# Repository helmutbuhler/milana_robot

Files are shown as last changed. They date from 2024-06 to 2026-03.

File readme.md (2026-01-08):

# Milana - A Two-Wheeled Jumping Robot

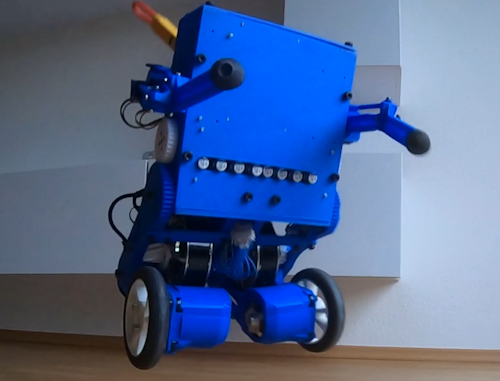
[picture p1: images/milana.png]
Milana


## Overview
Milana is a small and relatively cheap robot on two wheels. For a general description on how I built this robot, see [here](blog_post.md)

The robot has 6 motors on each side:
 - A BDC 280KV motor controlling the wheel.
 - A BDC 100KV motor controlling the knee (used for jumping).
 - A 35kg servo motor controlling the hip.
 - 3 1.5kg small servo motors, controlling the arm.

The brushless motors are controlled with two [ODrives](https://odriverobotics.com/), each with custom firmware to enable some of the tricks demonstrated in the [video](https://www.youtube.com/watch?v=lOAjTAtRaGs). All motors, except for the arm motors, also have precise encoders attached.
The robot is powered by two 3Ah 3S Lipo batteries and controlled by a Jetson Nano. The Jetson Nano is running custom control software on Ubuntu with a slightly modified Linux kernel. Beside the ODrives, the Jetson Nano is connected to the following:
 - IMU sensor for 3D Orientation.
 - Servo Driver to control all servo motors.
 - A2D Converter for battery charge measurement.
 - Microphone and speaker.

## Control
The robot can be controlled externally using various methods:
 - With custom software (Control UI), running on a separate computer and connected via Wifi. This can also be used to tune and calibrate internal parameters, debug issues and simulate certain parts of the robot.
 - With a wireless XBox controller.
 - With speech recognition and a [LLM](https://www.youtube.com/watch?v=1e_AJBxF1MY). The robot can reply using speech synthesis and execute a number of commands.

 ## Abilities
 The robot can...
 - balance on its wheels while driving and changing its body posture.
 - move its "knees" so fast that it will jump a few centimeters.
 - control each arm with 3 degrees of freedom and pick up light objects with them.
 - move up to about 10 km/h.
 - keep balance while moving with one wheel on a small ramp.

## Code
This robot is completely Open Source: The code for the "brain" of the robot is in this repository [in the robot folder](robot/). The software to control and debug the robot, [Control UI](control_ui/), is also here. There are also modules for [Automatic Speech Recognition](asr/), [Large Language Model](llm/) and [Text To Speech](tts/) included here that can optionally be used to have a conversation with the robot. Some of the code is in other repositories: The custom image for the Jetson Nano is [here](https://github.com/helmutbuhler/jetson_nano_image_milana). And the custom firmware image for the ODrives is [here](https://github.com/helmutbuhler/odrive_milana). All of these links point to a readme with more information about each component.

## Building
The CAD files and the meshes that need to be printed with a 3D printer are [here](CAD/). Other things that you need to buy are listed in the [Bill of Materials](extras/BOM.ods) (the total is about 1200€). [Here](images/) are some photos of the completed robot with some annotations for reference. More detailed information about each part is also in the comments of the code that controls it. 

This is not a project for beginners. If you intend to make the robot, some experience in robotics and coding is recommended. I also don't provide any warranty of any kind. Use all of this at your own risk.

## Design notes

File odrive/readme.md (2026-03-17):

# ODrive
## Overview
This robot uses two ODrives to control the 4 BLDC Motors that control the feet and leg motors. Some modifications were required to the Firmware, which you can find [here](https://github.com/helmutbuhler/odrive_milana). Clone that repository into the user home folder on the Jetson and flash the Firmware onto the ODrives (instructions are there).

The ODrive connected to the leg motors is located in the front of the robot (opposite of batteries). To connect to it with ODrivetool via UART, use this:
```
python3 ~/odrive_milana/tools/odrivetool --path serial:/dev/ttyTHS1_921600_8N2
```
Its axis numbers are: left=1 right=0

The ODrive connected to the foot motors is located in the back of the robot (same side as batteries). To connect to it with ODrivetool via UART, use this:
```
python3 ~/odrive_milana/tools/odrivetool --path serial:/dev/ttyS0_921600_8N2
```
Its axis numbers are: left=0 right=1

To connect to an ODrive via USB, use this:
```
python3 ~/odrive_milana/tools/odrivetool
```
After flashing the ODrive, you first need to configure them via USB before you can access them with UART. The robot body has holes on its sides where the usb ports on the ODrives are. So you can flash them without taking the robot apart.

In the following are the commands to initialize them with ODriveTool:

## Leg ODrive Initialization
Note: The requested_state assignment in the bottom will start motor calibration. Make sure the motors are free to rotate for that. The gears on the leg motors are designed in such a way that the motor becomes free when you rotate the leg all the way back. This way you don't have to detach the lower legs to calibrate the motors.
```
odrv0.erase_configuration()
odrv0.config.uart_baudrate = 921600
odrv0.config.uart_stop_bits = 2
odrv0.config.uart_use_ascii_protocol = False
odrv0.config.brake_resistance = 0
odrv0.config.max_regen_current = 0
odrv0.config.dc_max_negative_current = -15

odrv0.axis0.motor.config.current_lim = 10
odrv0.axis0.motor.config.pole_pairs = 20
odrv0.axis0.motor.config.torque_constant = 1
odrv0.axis0.motor.config.pre_calibrated = True
odrv0.axis0.motor.config.requested_current_range = 120
odrv0.axis0.encoder.config.abs_spi_cs_gpio_pin = 4
odrv0.axis0.encoder.config.mode = ENCODER_MODE_SPI_ABS_AMS #257
odrv0.axis0.encoder.config.cpr = 2**14
odrv0.axis0.encoder.config.use_index = False
odrv0.axis0.encoder.config.ignore_abs_ams_error_flag = True

odrv0.axis1.motor.config.current_lim = 10
odrv0.axis1.motor.config.pole_pairs = 20
odrv0.axis1.motor.config.torque_constant = 1
odrv0.axis1.motor.config.pre_calibrated = True
odrv0.axis1.motor.config.requested_current_range = 120
odrv0.axis1.encoder.config.abs_spi_cs_gpio_pin = 5
odrv0.axis1.encoder.config.mode = ENCODER_MODE_SPI_ABS_AMS #257
odrv0.axis1.encoder.config.cpr = 2**14
odrv0.axis1.encoder.config.use_index = False
odrv0.axis1.encoder.config.ignore_abs_ams_error_flag = True

odrv0.axis0.requested_state = AXIS_STATE_FULL_CALIBRATION_SEQUENCE
odrv0.axis1.requested_state = AXIS_STATE_FULL_CALIBRATION_SEQUENCE

# Make sure no errors occured:
dump_errors(odrv0, True)

odrv0.axis0.encoder.config.pre_calibrated = True
odrv0.axis1.encoder.config.pre_calibrated = True

odrv0.save_configuration()
```

## Foot ODrive Initialization
Note: The requested_state assignment in the bottom will start motor calibration. Make sure the motors are free to rotate for that.
```
odrv0.erase_configuration()
odrv0.config.uart_baudrate = 921600
odrv0.config.uart_stop_bits = 2
odrv0.config.uart_use_ascii_protocol = False
odrv0.config.brake_resistance = 0
odrv0.config.max_regen_current = 0
odrv0.config.dc_max_negative_current = -15

odrv0.axis0.motor.config.current_lim = 10
odrv0.axis0.motor.config.pole_pairs = 7
odrv0.axis0.motor.config.torque_constant = 1
odrv0.axis0.motor.config.pre_calibrated = True
odrv0.axis0.motor.config.requested_current_range = 120
odrv0.axis0.encoder.config.mode = ENCODER_MODE_INCREMENTAL #0
odrv0.axis0.encoder.config.cpr = 8192
odrv0.axis0.encoder.config.use_index = True
odrv0.axis0.config.calibration_lockin.vel = -40
odrv0.axis0.config.calibration_lockin.ramp_distance = -3.141592653589
odrv0.axis0.config.calibration_lockin.accel = -20

odrv0.axis1.motor.config.current_lim = 10
odrv0.axis1.motor.config.pole_pairs = 7
odrv0.axis1.motor.config.torque_constant = 1
odrv0.axis1.motor.config.pre_calibrated = True
odrv0.axis1.motor.config.requested_current_range = 120
odrv0.axis1.encoder.config.mode = ENCODER_MODE_INCREMENTAL #0
odrv0.axis1.encoder.config.cpr = 8192
odrv0.axis1.encoder.config.use_index = True
odrv0.axis1.config.calibration_lockin.vel = 40
odrv0.axis1.config.calibration_lockin.ramp_distance = 3.141592653589
odrv0.axis1.config.calibration_lockin.accel = 20

odrv0.axis0.requested_state = AXIS_STATE_FULL_CALIBRATION_SEQUENCE
odrv0.axis1.requested_state = AXIS_STATE_FULL_CALIBRATION_SEQUENCE

# Make sure no errors occured:
dump_errors(odrv0, True)

odrv0.axis0.encoder.config.pre_calibrated = True
odrv0.axis1.encoder.config.pre_calibrated = True

odrv0.save_configuration()
```

## Anticogging
To make the movement of the foot motors more smooth, Anticogging should be calibrated and enabled. The motors will work without this, but the balancing will work much better with Antocogging enabled. To learn more about Anticogging on ODrive, watch [this](https://www.youtube.com/watch?v=CWzuBoYLISY). Anticogging on the Leg motors could be theoretically enabled also, but because it has a 3 to 1 gear ratio you don't really notice the cogging there.

Use the following to run the calibration. The wheels must be free to rotate for this to work. I usually make the robot lay on its batteries and put the feet up in the air.
```
def start_anticogging_calibration(axis, vel_gain):
    axis.controller.config.control_mode = CONTROL_MODE_POSITION_CONTROL
    axis.controller.config.pos_gain = 100
    axis.controller.config.vel_gain = vel_gain
    axis.controller.config.vel_integrator_gain = 100
    axis.controller.config.anticogging.calib_pos_threshold = 1
    axis.controller.config.anticogging.calib_vel_threshold = 1
    axis.controller.config.anticogging.anticogging_enabled = False
    axis.motor.config.current_lim = 10
    axis.requested_state = AXIS_STATE_CLOSED_LOOP_CONTROL
    axis.controller.input_pos = 0
    print("init...")
    import time
    time.sleep(1)
    print("start_anticogging_calibration")
    axis.controller.start_anticogging_calibration()

start_anticogging_calibration(odrv0.axis0, 4)
start_anticogging_calibration(odrv0.axis1, 4)
```

You may need to tune the gains a little bit. Once both feet are calibrated, put them back into idle:
```
odrv0.axis0.requested_state = AXIS_STATE_IDLE
odrv0.axis1.requested_state = AXIS_STATE_IDLE
```

And save the calibration:
```
odrv0.axis1.controller.config.anticogging

odrv0.axis0.controller.config.anticogging.anticogging_enabled = True
odrv0.axis1.controller.config.anticogging.anticogging_enabled = True
odrv0.axis0.controller.config.anticogging.pre_calibrated = True
odrv0.axis1.controller.config.anticogging.pre_calibrated = True
odrv0.save_configuration()
```

You can optionally retrieve the calibrated values with the following. This is useful to debug encoder slippage.
```
def get_anticogging_map(axis, filename):
    with open(filename, 'w') as f:
        for i in range(3600):
            if i%100 == 0:
                print(i//100)
            val = axis.controller.get_anticogging_map(i)
            f.write(str(val))
            f.write('\n')
get_anticogging_map(odrv0.axis0, 'anticogging_map_0.csv')
get_anticogging_map(odrv0.axis1, 'anticogging_map_1.csv')
```

To check if the Anticogging is working, you can enable a constant slow speed in `control_ui` and plot the position. You can also enable/disable Anticogging there with a checkbox.
This Anticogging Calibration needs to be done only once because the feet have absolute encoders. If you notice that it's not working anymore after some time, or after a jump, you likely have encoder slippage.

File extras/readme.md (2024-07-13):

# Extra Files
## Overview
This folder has some documentation that didn't fit anywhere else.

## BOM
This is a spreadsheet with the Bill of Materials. You can open it with LibreOffice or with Excel.

## Linux Commands
This is a file that has some useful commands for the Linux Terminal.

## Lagrangian Simulation Derivation
In this folder are the jupyter notebooks that were used to derive the equations of motions for a triple-pendulum on a wheel. Those equations were then used in `control_ui/pendulum_simulation.cpp`, which is then used to simulate the robot. The comments in the corresponding header file also provide some context. See the comments in `control_ui/simulation_ui.cpp` on how to use the simulation.

The notebooks are these two files:
```
eulerlagrangian_cartpole.ipynb
eulerlagrangian.ipynb
```
The first one is a simplified version that just covers the classic Cart Pole. The second one derives the full equations that simulate the robot.

To try out these notebooks, you need a suitable Python environment. I used Anaconda with this Environment:
```
conda create -n sympy python=3.10
conda activate sympy
conda install -c anaconda sympy jupyter
```
But something similar with pip will probably also work. You can also try to open them directly with VS Code. See [here](https://www.dataquest.io/blog/jupyter-notebook-tutorial/) on how to use Jupyter Notebook.

The Lagrangian Method is used in those notebooks. It is explained [here](https://scholar.harvard.edu/files/david-morin/files/cmchap6.pdf), alongside some examples that explain how to apply this method manually.

The triple-pendulum is a straightforward extension of the double-pendulum, and there is a lot of information about that out there. [Here](https://scipython.com/blog/the-double-pendulum/) is a well described simple python implementation.

The wheel attached to the pendulum is very similar to a cart attached to a pole. And the Cart Pole is also something well researched. A good explanation is [here](http://piepieninja.github.io/2019/05/09/cart-pole-dynamics/) and [here](https://www.matthewpeterkelly.com/tutorials/cartPole/index.html).

A combination of a double-pendulum with a cart is covered [here](https://www3.math.tu-berlin.de/Vorlesungen/SoSe12/Kontrolltheorie/matlab/inverted_pendulum.pdf). It also contains a MatLab assisted derivation of its equations of motions.

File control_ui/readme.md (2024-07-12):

# Control UI
[Control UI demo](https://github.com/user-attachments/assets/ef9a0bbf-39a2-4dd6-9c05-335df541d1d5)

## Overview
control_ui is an application that connects to the robot via WIFI and gives you a lot of features:
- Control the robot via keyboard (arrow keys to move, P, L, O, K to move joints)
- Monitor about 300 variables received by the robot. Displayed as plots.
- Control lots of variables on the robot (tune pid controllers etc.)
- Display usb webcam data and sync it to the data received from the robot.
- Display sensor state in 2D and 3D models of the robot.

When not connected to the robot, this can also be used to run simulations of the robot
(mainly of the movement of the wheels) and to debug IK stuff.
It can also be used to load capture data that was saved to a file earlier.

Note that the robot can also work when control_ui is not connected to it.

[ODrive Control UI](https://github.com/helmutbuhler/odrive_control_ui) is a repository with a trimmed down version of this application. This might be a better starting point for new projects.

The video above shows the application in action while the robot jumps. The ODrive oscilloscope is used there to retrieve precise position data of the motors that trigger the jump. You can also see the different jump states in the plot there. The plotting data of that run is in this repository, in case you want to take a look yourself.

## Build
### Windows
To build on Windows, you need VS2019 or up. Clone this repository and open `milana_robot.sln`. It should build out of the box.

### Linux
To build on Linux, first we need some packages:
```
sudo apt install cmake libglfw3-dev libglm-dev libusb-1.0-0-dev libasound2-dev build-essential gnome-terminal
```

Next clone the repository, cd into it and do this:
```
mkdir build
cd build
cmake -DCMAKE_BUILD_TYPE=Release ..
make
```
If you get errors involving ASR and Cuda, comment that project out of the `CMakeLists.txt` file. See in the `asr` folder on how to compile that part.

Once it's compiled you can start Control UI with:
```
./control_ui
```

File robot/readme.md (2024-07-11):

# Robot application
## Overview
This is the application that runs on the Jetson Nano inside of the robot and controls pretty much all of the components.

The components correspond the the .cpp files here:
- asr_client
- balance_control
- battery
- body_acc
- command
- foot_control
- ik
- imu
- joystick
- leg_control
- main
- pin
- server
- servo
- statistics
- tts_client

More details about them is in the comments in the source.

The application has a main loop that runs at about 60Hz and updates all the components in each iteration. It's defined in `main.cpp`. You will notice there that all the components are very independent of each other. It's easy to disable them individually. This is very helpful for testing things. Initially you will want to comment them all out, except for the server, and test network connection with Control UI. After that works you can uncomment them step by step.

## Jetson Nano Configuration
You need to install the custom [Milana Image](https://github.com/helmutbuhler/jetson_nano_image_milana) on your Jetson Nano so that both UART ports work (we need those to communicate with the ODrives). It's also required to make the SPI and I2C ports more reliable. Detailed instructions on how to install it are there.

Once you have that installed and established SSH via a WIFI connection, we need to configure it a bit more:

We need some packages: (We need python so that ODriveTool will work)
```
sudo add-apt-repository ppa:team-gcc-arm-embedded/ppa
sudo apt-get update && sudo apt-get install gcc-arm-embedded openocd git-lfs python3 python3-yaml python3-jinja2 python3-jsonschema meson portaudio19-dev python3-pip libopenblas-dev minicom nano

pip3 install PyYAML Jinja2 jsonschema requests pyusb intelhex appdirs ipython pyserial
sudo -H pip3 install -U jetson-stats
```

We also need to enable the SPI pins (for communication with the IMU) and the I2S pins (for communication with the MAX98357A board that controls the speaker):

```
sudo /opt/nvidia/jetson-io/jetson-io.py
Configure 40 pin
Configure header pins manually
enable i2s4 and spi1
Save pin changes
Save without reboot
```

And we need to initialize the audio driver once:
```
alsactl init
```

## Build
Building this application can be done directly on the robot with CMake, or indirectly through Visual Studio.

### CMake
Clone this repository on your Jetson Nano, cd into it and do this:
```
mkdir build
cd build
cmake -DCMAKE_BUILD_TYPE=Release ..
make robot
```
If you get errors involving ASR and Cuda, comment that project out of the `CMakeLists.txt` file. We don't need the ASR Server on the Jetson Nano.

Once it's compiled you can start it with:
```
sudo ./robot
```
You can also test compilation on a Desktop Linux or in WSL. But it will obviously not run there.

### Visual Studio
To build from a Windows machine, you need VS2019 or up. Clone this repository on your Windows machine and open `milana_robot.sln`. The project `robot` in there is a "Raspberry" project which is built remotely on our Jetson Nano. You need to install the `Linux Development with C++ workload` workload in Visual Studio for this to work. I found it convenient to build this way because you can develop on a real PC and it only needs to upload the changed files. See [here](https://devblogs.microsoft.com/cppblog/linux-development-with-c-in-visual-studio/) for more information.

If you get build errors, copy this folder `3rdparty/eigen` from the repo into: `~/projects/3rdparty/eigen` (I didn't figure out how to do this automatially).

After a successful build, you need to start the application through ssh:
```
sudo ~/projects/robot/bin/ARM64/Release/robot.out
```
(Starting and Debugging from Visual Studio won't work because the application needs sudo rights)

You can optionally define an alias, so you just need to type `robot`:
```
nano ~/.bashrc
# append the following:
alias robot="sudo ~/projects/robot/bin/ARM64/Release/robot.out"
# reload .bashrc
source ~/.bashrc
```

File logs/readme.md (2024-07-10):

# Control UI Log Files
Here are log files that can be saved and loaded with Control UI.

I put a small example file with video data here where the robot jumps. Note that the right leg encoder seems to have malfunctioned in this jump a little bit and caused the robot to think that is started landing before it actually did. It still did land successfully though somehow.

I limited the file to the actual jump to save some space (these files can get quite huge).

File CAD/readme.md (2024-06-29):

# CAD

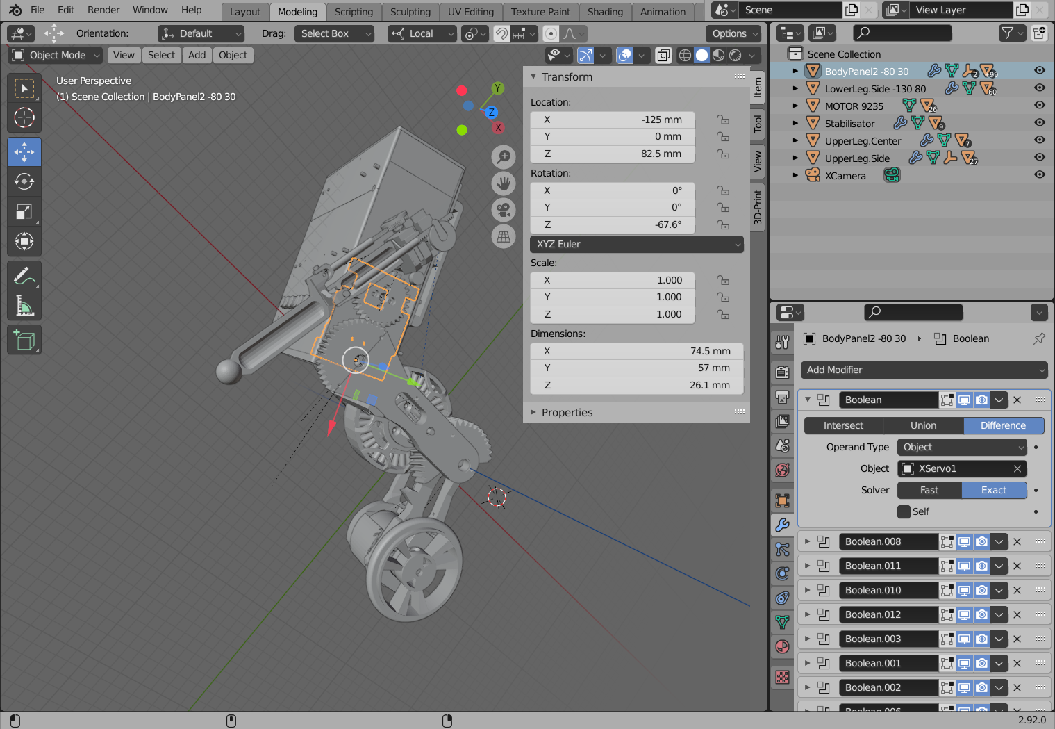
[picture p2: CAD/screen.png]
Blender screenshot


## Overview
Here are the blender files that I used to plan the robot and to print all the parts.

`Robot.blend` contains almost all parts, except for the wheel, the arm and the encoder adapter for the foot motor. Those are in separate files. Since the robot is mostly symmetrical, I only designed the left side for most mirrored parts. Blender isn't exactly a typical CAD software, but I wanted to try it out for this project anyway and it worked quite well.

If you want to use blender to modify these files or to create your own, I recommend to install some plugins: The [blender-apply-parent-inverse](https://github.com/drewcassidy/blender-apply-parent-inverse) blender plugin allows you to reset the internal matrix blender uses in its object tree. I also used this [Blender-Gear](https://github.com/xynium/Blender-Gear) addon to create the gears. I made screenshots of the settings I used to create the gears, just in case they need to be modified (not exactly elegant, I know).

## Printing
If you just want the parts that need to be printed, I exported those in the `Meshes` folder. Some parts need to be printed double, those have `_double` in the filename. And some parts need to be printed also twice, but one time mirrored. Those have `_mirror` in the filename. Some parts need to be made out of rubber. The negative forms used to create them are here as well, they have `rubber_negative` in the filename.

In total it's about 60 parts that need to be printed. I suggest starting with the body, then the legs. When everything is working, you can add the arms. 3D printers arn't super precise, you will probably need to adjust some parts in blender if they don't fit. Some parts need to be printed with support. I used [Cura](https://ultimaker.com/de/software/ultimaker-cura/) to slice the meshes, but it probably doesn't matter which software you use for that.

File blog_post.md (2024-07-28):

# Creating a Two-Wheeled Robot - And How to Teach it to Jump
In this "Blog Post", I want to demonstrate the challenges I faced while making this robot and explain the history of it a bit. I don't have an actual blog, so I'll just host it here on Github, together with the Source Code of the project.

It all started when I learned about [Raspibotics MABEL robot](https://raspibotics.wixsite.com/pibotics-blog/post/01-build-a-self-balancing-robot-with-legs-boston-dynamics-handle-inspired), together with a list of materials and a description how to build it. I've always been interested in Robotics and this guide seemed like a good place to start. I also had some extra time due to Corona. My goal was to rebuild this MABEL robot, and then to improve upon it. The robot is basically a small version of [Handle by Boston Dynamics](https://www.youtube.com/watch?v=-7xvqQeoA8c) but lacks some of its features: Jumping, moving on a ramp and grabbing things. I wanted to add these features.

Building MABEL went surprisingly smooth. I bought a 3D printer, learned some electronics, learned how to do some basic 3D modeling in blender and wrote some code that I put on a Raspberry Pi and connected everything together. You can see the initial version below (right) next to my inspiration (left):

MABEL Inspiration
Initial Version GIF

You can't see it balancing there, but it has stepper motors on the wheels and a total of 4 servo motors for its "legs". Getting the robot to balance wasn't difficult. You put in an IMU sensor, implement a so called PID controller and tune 3 parameters until it balances. There are a lot of resources out there that explain this in detail.

The difficult part is what you don't see in the video: the jumping. The servo motors move with maximum speed in that video. And the wheels don't even leave the ground. I realized then that I needed completely different motors. Unfortunately I didn't know much about motors back then. So I started experimenting a bit. I took a brushed motor with a built in gear (those a very cheap and easy to use) and tried to load a spring with it. Once the spring is released, it could use all the stored energy at once for the jump. Kangaroos use a similar trick to jump, so it should work right? 

Spring GIF

As you can see above, it didn't work at all. Again, the feet didn't even leave the ground. And the body of the robot wasn't even attached yet. It was clear then that my intuition about this was completely off and I decided to simulate it before actually building it. Making a simulation takes some time, but it would quickly pay off. You can try out lots of different motors and robot designs much faster than building it for real. I briefly tried to build a physics engine from scratch for this, after all, how difficuilt can it be to simulate a little robot? Well, the math was too hard, so I gave that up pretty quickly. I also searched for what people in the robotics industry use, but I couldn't find anything that was lightweight and free. I had some experience with 3d physics engines at that point, but I was a bit reluctant to use those. I didn't really need a 3D simulation for this, the robot can be easily reduced to 2 dimensions if you just care about the jumping. And all the 3D math and collision detection would complicate things quite a bit. Luckily I found out about [Box2D](https://box2d.org/), a lightweight 2D physics engine. It's primarily made for games, but I figured it would be accurate enough for this. And it was surprisingly simple to use. All I needed to do was to calculate the torque output for a given motor and current and recreate the robot in that simulation environment. I also checked that the simulation was sufficiently accurate with [Stanford Doggo](https://github.com/Nate711/StanfordDoggoProject) (a robot which [jumps on for legs](https://www.youtube.com/watch?v=YeUpceVrUfg)). That's an Open Source robot with all motor specs published, so I could simulate that robot and check that the jump height in the simulation matches the one in the video. And it did actually match. I had to use a very small delta time step, it was much slower than realtime, but the accuracy seemed pretty good.

With the simulation environment running and validated, the rest was pretty easy. I evaluated a couple of motors, varied the gear ratio and leg length a bit and then compared the cost of the motors to the jump height. This is the simulation of the configuration I decided to build: 

Jump Simulation GIF

It uses motors similar to what Stanford Doggo uses: Two brushless motors with a gear ratio of 3 to 1, controlled by an [ODrive Motor Controller](https://odriverobotics.com/).

Actually fitting the ODrive inside of the robot body and attaching the motors to the legs required quite a bit of modelling and printing, but the first prototype with one motor looked pretty promising:

BLDC Test Jump GIF

We have successfully lifted off! Not much, and I still had to hold it a bit for balance and catch it after the jump. But fixing that would be easy, right?

Well, once fully assembled, the very first recorded jump was actually successful:

Jumping GIF

But that turned out to be a fluke. This initial version was so unreliable at jumping, it would only successfully land maybe 1 out of 10 times. Improving that successrate would turn out to be very difficult. [Here](https://8gadgetpack.net/milana/jump_fails8.gif) is a small compilation of some of the many many test jumps, that wern't quite successful. Can you see why those jumps failed and how to fix it? If so, you are smarter than I am. I needed more information to debug these issues, and a conventional debugger is of little help here.

What I ended up doing is to write some software that connected to the robot via WIFI and queried its internal state (which updates roughly at 60Hz). This sofware was also recording these jump attempts with a webcam (also captured with 60Hz) and then displayed all this information in a plotting window. This software also has special handling of ODrive data. ODrive updates at 8000Hz, much faster than the main loop on the robot. ODrive needs to be this fast because it needs to control the current in the 3 wires of the motor very quickly, but sadly communication between the ODrive and the main computer is so slow that it cannot be queried in realtime. In order to still get that information with full precision, I had to store that data on its internal (very limited) RAM during the jump and then retrieve it from there after the jump.

In the end, such a plot of a successful jump looks something like this:

Jump with Plots GIF

You can see the sensor readings of all the motors visualized as 2d and 3d models at the top. The angular position of both jumping motors is also plotted out.

This software helped me a great deal to make the jumps more reliable. One trick that helped a lot is to align both legs during the jump in such a way that they will touch the ground simultaneously. The robot will always slightly rotate to the left or right, but by moving the legs this can be compensated. Of course, you need to detect in which way the robot rotates. The built in accelerometer won't help here, you are weightless in free fall. But if you query a gyroscope with around 400Hz and make no mistakes in the 3d rotation math, you get pretty accurate results.

Another trick is to explicitly separate the time during a jump into different states. You can see the separate states in the video above visualized as a blue stairstep. I won't go into detail what all the states mean, but an interesting state transition is between falling and landing. While falling, you want to apply a lot of force to the motors, so that they can reach the correct position that is required for landing. Once landing with the ground is detected, you need to adjust the force in such a way that results in a smooth landing. If you apply too much force, the wheel might bounce off the ground. If you use too little force, the lower leg will rotate until it hits the upper leg and not slow down the robot in time. (In the landing part, the plot above is a bit crude. Thats where the ODrive RAM ran out and only data at 60Hz is available)

Another thing that became apparant in these recorded videos was that the initial motors that control the wheels were too weak. I replaced those with brushless motors and added a second ODrive to control them to fix this. I also had trouble finding rubber wheels that have sufficient grip with the ground. I ended up making my own with a 3d printed mold, similar to what James Bruton did in [this video](https://youtu.be/eKZIJwJBjEs?t=540).

An interesting issue that sometimes arose was that the robot would jump and land perfectly, but then lose balance and move either forwards or backwards until it fell down. It was clear that this was a PID Controller issue, the hardware was working perfectly fine. But I was at a loss how to fix it. Changing the gains didn't work, and experimenting with hacks to fix this wasn't very productive. Each unsuccessful fall could break something. And fixing things takes a lot of time. I decided to simulate this part of the robot as well, just to figure out whats's wrong with the PID algorithm. I didn't want to use Box2D for this though. At this time, it became apparant that something must be wrong with that simulation. The actual jump heights didn't come close to the simulated ones. So I bit the bullet and learned the math for physics simulations. And it turned out to be much simpler than thought. What you use is the so called "Lagrangian Method". It's something physics students learn. But if you are just interested in the results, it's enough to define an Energy function for a given robot state, let some numeric system differentiate and simplify some formulas, and voila: You get a linear equation that you solve at runtime and you get an acceleration for each timestep. Sounds fancy, but the difficult part really was just finding software that does the differentiation for you, all you need to provide is the kinetic and potential energy for a given robot state (few lines of python code, and similar to the double pendulum). And the resulting simulation was not only fast, it was very accurate. I could directly compare it to my recorded jumps, and it matched very well. With these simulations, it was also easy to find out the problem: When the motor cannot realize the commands of the PID controller, the integral would grow very fast and cause this issue. Now that I knew what to look for, I found the search term for it: [Integral Windup](https://en.wikipedia.org/wiki/Integral_windup). And one of its well known solutions, Backcalculation, worked like a charm to fix this. I made a little demonstration here that shows Backcalculation in action (simulated, but very similar to reality):

Backcalculation GIF

This plots the commanded velocity (blue), the control velocity (orange) and the realized velocity (brown).
You can see that the initial graph looks very similar, with and without Backcalculation. But the inserted sudden rotation in the last third can only be handled with Backcalculation. So yeah, it took me some time to find the cause of this problem. And the solution is implemented in one line of code. But at least I found a proper solution.

On the hardware side, I didn't always find one of those: The encoders, the devices that measure the angle of the joints, need to be very accurate so that the motor controller can work. Unfortunately, the strong acceleration while jumping and landing caused the internal structure of these encoders to slip along the axis. I found a solution involving glue and burning plastic with a soldering iron, but it wasn't pretty. EM Noise also was a serious issue. Due to the heavy current the motors require while jumping and the close space due to the robots small size, I had lots of Heisenbugs and data corruption problems. I got them down pretty good by hacking some of the Linux kernel, the ODrive firmware and using insulated wiring, but I'm still not super happy with it.

In the end, I got the jumping to work pretty reliably. It doesn't jump as high as I initially simulated or hoped, but I guess that's good enough.

Jump Simulation and real Jump GIF

I also implemented other features than jumping. It can balance while moving with one leg on a ramp. I added some arms with some Inverse Kinematics control. And I also added a way to communicate with the robot via voice and a local ChatGPT clone (see [here](https://www.youtube.com/watch?v=1e_AJBxF1MY)). But this post is getting long enough, so I just refer to the code and readmes in this repository and this [Youtube Video](https://www.youtube.com/watch?v=lOAjTAtRaGs).

All in all, I believe it's fair to say that this robot is very similar feature wise with Boston Dynamics Handle Robot. Although I admit that it doesn't look as fancy and isn't quite as elegant, but I'm still quite happy with it.

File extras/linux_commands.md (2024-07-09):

# Linux Commands
## Overview
Here are some commands that might come in handy. You can use them once you are connected to your Jetson Nano via ssh/putty.

## Basic stuff

Shutdown: `sudo shutdown now`

Reboot: `sudo reboot`

Change dir: `cd xxx`

List files: `ls`

Edit file: `nano xxx`

## List all USB devices

Run this to list all connected USB devices.
```
lsusb
```

## Show Nvidia Jetpack version
```
head -1 /etc/nv_tegra_release
sudo apt-cache show nvidia-jetpack
```

## Show CPU usage
```
jtop
```

## Change Linux bootloader commandline
```
sudo nano /boot/extlinux/extlinux.conf
```

## Check I2C open addresses
```
i2cdetect -y -r 1
```
Open addresses should be:

IMU: 0x53 0x0F 0x68

Servo: 0x40, 0x70

A2D: One of the following: 0x48  (-), 0x49  (+), 0x4A  (SDA), 0x4B  (SCL)

## SPI
List loaded spi devices:
```
ls /dev/spi*
```

Test SPI:
```
wget https://raw.githubusercontent.com/torvalds/linux/v4.9/tools/spi/spidev_test.c
gcc -o spidev_test spidev_test.c
# Place a jumper to short pins 19 & 21 on the Jetson Nano 40 pin header (for SPI1), then run spidev_test with the following command:
./spidev_test -D /dev/spidev0.0 -v -p "HelloWorld123456789abcdef"
```

If SPI is not working, check GPIO status:
```
sudo cat /sys/kernel/debug/tegra_gpio
```
The first lines should look like this:
```
Name:Bank:Port CNF OE OUT IN INT_STA INT_ENB INT_LVL
 A: 0:0 64 40 40 04 00 00 000000
 B: 0:1 00 00 00 00 00 00 000000
 C: 0:2 00 00 00 00 00 00 000000
```

## Show GPIO state
```
sudo cat /sys/kernel/debug/gpio
```

## Change I2C frequency
```
sudo nano /sys/bus/i2c/devices/i2c-1/bus_clk_rate
```

## List and kill processes
```
sudo ps -a
# kill all robot.out processes:
sudo killall -9 robot.out
# kill specific pid:
kill -9 *pid*
```

## Used diskspace / diskusage, RAM usage:
```
ncdu -x /
df -h
# ram usage:
free -h
```
## Free docker diskspace
```
sudo docker system prune -a
```

## Debugging with GDB

Attach to running process:
```
# find process id:
pgrep robot
sudo gdb -p *pid*
```

Start robot with debugger:
```
sudo gdb ~/projects/robot/bin/ARM64/Debug/robot.out
run
```

Show info about threads:
```
info threads
```

Show code in crappy GUI:
```
tui enable
```

Useful commands while debugging:

`c` - Continues running the program until the next breakpoint or error

`s` - step into function

`n` - step over into next line

`fin` - step out

`u N` - step until linenumber N

`p var` - Prints the current value of the variable "var"

`bt` - Prints a stack trace

`q` - Quits gdb

`b` - Add breakpoint on function or linenumber

## Find/Search files
Find *jpg files in home:
```
find /home -name *.jpg  2>/dev/null
```

find big files on filesystem:
```
sudo du -sx /* 2>/dev/null | sort -n
```

## Serial/UART testing
start serial console to test tts:
```
minicom -b 921600 -D /dev/ttyTHS1
minicom -b 921600 -D /dev/ttyS0
```

List UART ports:
```
dmesg | grep -i THS
```

## Kernel log
```
tail -F /var/log/kern.log
```

## Connect WIFI
Status: `nmcli d`

List wifis: `nmcli dev wifi`

List known wifis: `ls /etc/NetworkManager/system-connections`

Rescan: `sudo nmcli device wifi rescan`

Delete connection: `sudo nmcli con delete "xxx"`

Enable: `nmcli r wifi on`

Connect: `sudo nmcli d wifi connect wifi_name password xxx`

(reboot if connection fails or no wifis are listed)

Disable wifi temporarily: `ifconfig wlan0 down`

## Configure bash alias
```
nano ~/.bashrc
alias robot="sudo ~/projects/robot/bin/ARM64/Release/robot.out"
# reload .bashrc:
source ~/.bashrc
```

## UART init:
```
sudo systemctl stop nvgetty
sudo systemctl disable nvgetty
udevadm trigger
# Allow non-root users access to UART:
sudo adduser *username* dialout
sudo chmod 666 /dev/ttyS0
sudo chmod 666 /dev/ttyTHS1
```

## Make I2C speed configurable without sudo
Source is [here](https://unix.stackexchange.com/a/409780)
Create this file with the following content:
```
/etc/systemd/system/bus_clk_rate_permissions.service
```
```
[Unit]
Description=bus_clk_rate writable to everybody

[Service]
Type=oneshot
User=root
ExecStart=/bin/bash -c "/bin/chmod 666 /sys/bus/i2c/devices/i2c-1/bus_clk_rate"

[Install]
WantedBy=multi-user.target
```

Then run this:
```
sudo systemctl enable bus_clk_rate_permissions.service
sudo systemctl start bus_clk_rate_permissions.service
sudo systemctl status bus_clk_rate_permissions.service
```

## Install nvidia docker
On VM:
```
sdkmanager --cli --query interactive
```
(Select option 1 and login via nvidia account)

Select these options:
```
- select product: Jetson
- hardware configuration: Target Hardware
- select target: Jetson Nano modules
- select target operating system: Linux
- select version: JetPack 4.6.4
- get detailed options: Yes
- select Jetson SDK Components
- flash the target board: No
```
Install stuff on your Nano? Select Install
- Connect via ethernet cable
- IPv4
- Type in IP of Nano (find out on Nano via ifconfig)

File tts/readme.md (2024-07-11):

# TTS Server

## Overview
Here is the code for running the TTS Server. It allows the robot to convert text into speech. The protocol is very simple: it receives the text and sends the audio signal back. Sadly I didn't find a way to make this application native, it uses Python.

There are two implementations here of this server:
- Implementation based on [StyleTTS 2](https://github.com/yl4579/StyleTTS2). It must run on a separate machine with a gpu and is much faster, has better quality and is easier to set up than the other implementation.
- Implementation based on [Coqui TTS](https://github.com/coqui-ai/TTS.git). This one can run locally on the Jetson Nano. But it is a bit slow and quite difficult to set up. It needs to run in a docker container to make use of Jetsons acceleration hardware.

## StyleTTS 2

This implementation requires Python, either on a Linux or Windows machine. I used [Anaconda](https://www.anaconda.com/download) to create a Python Environment and used this to install the dependencies:

```
conda create -n tts
conda activate tts

conda install conda-libmamba-solver
conda install python=3.11 mamba -c conda-forge --solver=libmamba

# pytorch - current nightly works w/ Python 3.11 but not 3.12
# pick your version here: https://pytorch.org/get-started/locally/
mamba install pytorch torchvision torchaudio pytorch-cuda=12.1 -c pytorch-nightly -c nvidia

# reqs - torch stuff already installed 
pip install SoundFile munch pydub pyyaml librosa nltk matplotlib accelerate transformers phonemizer einops einops-exts tqdm typing typing-extensions git+https://github.com/resemble-ai/monotonic_align.git
python -m nltk.downloader punkt
```
(This is partly based on this [Guide](https://llm-tracker.info/books/howto-guides/page/styletts-2-setup-guide))

Next we need to clone [StyleTTS 2](https://github.com/yl4579/StyleTTS2) into the tts/style_tts2 folder and download its model files:
```
cd tts/style_tts2
git clone https://github.com/yl4579/StyleTTS2.git
# (I got Revision: cc4025cd69462b33c834d4b87dfaf307e9fe29bf, but master probably works, too)
cd StyleTTS2

# get models (gdown may not work, try manually downloading it in browser then)
pip install gdown
gdown 'https://drive.google.com/file/d/1K3jt1JEbtohBLUA0X75KLw36TW7U1yxq/view?usp=sharing'
unzip Models.zip

# (optional, if you want to experiment with the notebook)
mamba install jupyter notebook
```
On Windows, we also need to download eSpeak NG into `tts/style_tts2/eSpeak NG` from [here](https://github.com/espeak-ng/espeak-ng/releases/tag/1.51).

Finally we can start the server:
```
cd tts/style_tts2
python Inference_LJSpeech_Server
```

## Coqui TTS

Running [Coqui TTS](https://github.com/coqui-ai/TTS.git) on the Jetson Nano is a bit difficult: The Ubuntu version on the Jetson Nano only supports Python 3.6, which means that we need to use an older version of Coqui TTS. Also installing Pytorch (which Coqui TTS needs) is basically impossible without a Docker Container.

I forked the version of Coqui TTS that still works with Python 3.6 [here](https://github.com/helmutbuhler/TTS). It also includes some bugfixes. Clone it into `tts/coqui_tts`.

To create the Docker container, run:
```
cd tts/coqui_tts
./build.sh
```
If you don't have docker installed on your Jetson Nano, you need to install it with the sdkmanager. Building the image can take about 30 minutes and requires about 15GB of diskspace. So make sure to have a big enough SD card installed.

Once it is build, you can run it with:
```
cd tts
coqui_tts/run.sh
```
It will download the required models automatically on the first run. After it has done so, it will also work offline.

## Other TTS libraries
Here are some other libraries that I tried:
```
https://github.com/dusty-nv/jetson-voice
https://github.com/snakers4/silero-models#text-to-speech
https://r9y9.github.io/deepvoice3_pytorch/
https://github.com/neonbjb/tortoise-tts
https://github.com/suno-ai/bark
```
All of them are either too slow or too unreliable for the Jetson Nano.

## Note
The `elevatormusic_mono.wav` file in this folder is used by the robot to indicate that a response is coming soon. It's from [here](
https://pixabay.com/music/bossa-nova-waiting-music-116216). `finish.wav` is used to indicate that the response is finished (the file is from `alarm07.wav` in the Windows Media folder).

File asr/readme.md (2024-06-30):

# Automatic Speech Recognition Server

## Overview
This is a server that gives the robot access to Automatic Speech Recognition (optionally with a LLM).

The server basically does this:
- Receives audio samples.
- Passes those audio samples to [whisper.cpp](https://github.com/ggerganov/whisper.cpp) (the [model](https://github.com/openai/whisper) from OpenAI) to translate it into text.
- Optionally passes that text into a LLM to generate a text response (using [llama.cpp](https://github.com/ggerganov/llama.cpp)).
- Returns either the original text or the response back to the robot.

Not everything what is heard in the input audio stream is processed. First a passphrase must be said ("OK, Milana"), then the following audio is further processed until silence is detected for a few seconds.

This passphrase detection, and the silence detection, is done with a small whisper model (ggml-small.bin). Once a passphrase is detected, the audio after the passphrase is processed with a bigger model (ggml-large-v3.bin).

I ran this on a NVIDIA GeForce RTX 2080 Ti with 11GB. If you want to run it with a LLM, you need at least that much GPU memory. You also need about 32HB of RAM. Sadly, the Jetson Nano isn't capable of running this.

This program can optionally be built so that is receives audio directly from the local PC. See the defines at the top of `asr_server.cpp`.

You need to download some models to use this. Go to the models folder for more details.

## Build
You can build this on Windows, Ubuntu on WSL or on a real Ubuntu.

### Windows
Download and install the [NVidia Cuda Toolkit](https://developer.nvidia.com/cuda-downloads). Open `milana_robot.sln` in Visual Studio 2019 or up and it should build everything.

### Ubuntu
If you want to use WSL, you need to give WSL access to more RAM. Open `C:\Users\*username*\.wslconfig` and add this:
```
[wsl2]
memory=30GB
```
You also need to [install Cuda](https://developer.nvidia.com/cuda-downloads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) in WSL.

If you want to use the real Ubuntu, install the nvidia driver and cuda-toolkit with:
```
sudo apt install nvidia-cuda-toolkit nvidia-cuda-toolkit-gcc
```
See [here](https://www.cherryservers.com/blog/install-cuda-ubuntu) if that doesn't work.

Next you need to adjust the CUDA_ARCHITECTURES number in `CMakeLists.txt`. Find out your gpu capability by running:
```
nvidia-smi --query-gpu=compute_cap --format=csv
```
Then enter that number without the dot after CUDA_ARCHITECTURES in `CMakeLists.txt`.
After that go to the root of the repository and build it with:
```
mkdir build
cd build
cmake -DCMAKE_BUILD_TYPE=Release ..
make
```

And run it with `./asr_server`

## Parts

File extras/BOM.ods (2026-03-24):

Bill of Materials, as of 2024. Due to inflation and chip shortage, a lot of it has gotten much more expensive than what I paid for it. Also, some products have gotten discontinued.
But I have found alternatives for everything and linked them here. Not included in this list are some basic utilities (wrenches), Computer equipment and the 3D printer.
If you don't have access to a 3d printer (check local makerspaces and schools) I recommend buying one and selling it afterwards. It's much cheaper than online services that print stuff for you.
Item | Amount | Cost per Unit € | Cost Eur (estimate) | Url1 | Url2 | Desc
Screws
Cylindrical screws DIN 912 M3 12mm | 30 |  | 12 | https://www.ebay.de/itm/305239547189?itmmeta=01HY94NS4T2T8HYF5DXAR8V3HT |  | To fixate both ODrives, both custom platines, both leg encoders
Countersunk head screws DIN 7991 M3 10mm | 10 |  | 10 | https://www.ebay.de/itm/305239547189?itmmeta=01HY94NS4T2T8HYF5DXAR8V3HT |  | Fixate all AMS CUI encoders and the 2 gears on the servos for the hip
Cylindrical screws DIN 912 M5 16mm | 20 |  | 11 | https://www.ebay.de/itm/263447042776?itmmeta=01HY95KAX223SGS8Z4P0MFRAKM |  | Fixate body parts
Cylindrical screws DIN 912 M4 16mm | 24 |  | 9 | https://www.ebay.de/itm/263447042776?itmmeta=01HY95KAX223SGS8Z4P0MFRAKM |  | Fixate foot motor to 3d part, fixate stabilizer on upper leg, fixate hip servos to 3d part.
Cylindrical screws DIN 912 M5 25mm | 6 |  | 10 | https://www.ebay.de/itm/263447042776?itmmeta=01HY95KAX223SGS8Z4P0MFRAKM |  | Fixate on upper leg: hip-axis, gear of leg-motor and knee joint.
M2.5 x 6 Bottonhead | 10 |  | 4 | https://www.ebay.de/itm/134353157279 | https://hobbyking.com/de_de/titanium-m2-5-x-6-bottonhead-hex-screw-10pcs-bag.html | For fixating Jetson Nano and Absolute Encoders for leg motor (use only 3 screws for each encode)
Miniature flange ball bearings 5 X 10 X 4 mm | 10 | 1 | 10 | https://www.ebay.de/itm/264094750936 | https://www.ebay.de/itm/371591103683 | Ball bearings for joints and gears on the Upper Leg
Metal Servo Arm 25T Disc Metal Horns | 2 |  | 7 | https://www.amazon.co.uk/dp/B07G5BTMJB |  | Metal plate to fixate hip servos to gear.
Electronics
ADS1115 16-Bit ADC - 4 Channel via I2C | 1 | 3 | 3 | https://www.adafruit.com/product/1085 | https://www.ebay.de/itm/166044142289 | AD Converter for measuring battery power. Attached to the main custom platine.
USB to USB Isolator Board | 1 | 9 | 9 | https://www.ebay.de/itm/385400740608?itmmeta=01HY948EJYKM35GP61GRVMF2FZ | https://www.ebay.de/itm/314942449842?itmmeta=01HY946RY1F78PKVRQHR746F8K | For flashing ODrive via USB
IMU LSM6DS3 Digital Gyro SPI | 1 | 4 | 4 | https://www.ebay.de/itm/285830995436 |  | IMU sensor, on small custom platine next to Jetson. Connected to Jetson via SPI
2x40 Pin Header | 1 | 2 | 2 | https://www.ebay.de/itm/166757615561
PCB Boards | 1 | 5 | 5 | https://www.ebay.de/itm/125205128253 | https://www.ebay.de/itm/126468490871 | 7x9cm for main custom platine and 2x8cm for small custom platine
PCA9685 16-Channel 12-bit PWM Servo motor Driver I2C | 1 | 6 | 6 | https://www.ebay.de/itm/385488387798 | https://www.ebay.de/itm/255283290226 | Servo motor driver. Mounted on main custom platine
LMS2596 Buck Step-down DC-DC Power Converter | 2 |  | 3 | https://www.ebay.de/itm/404292803182 |  | Voltage converter, both on main platine. One for 5V powering Jetson and I2C components. One for 6V, powering the Servos
2 custom PSB Isolators with ISO7762FDW | 2 |  | 10 | https://discourse.odriverobotics.com/t/ots-opto-isolator-for-uart-ground-loop/5810/6 | https://discourse.odriverobotics.com/t/isolating-motors-power-from-controller-sensors-power-demands/9524 | Need to order 3 boards (need just 2) from oshpark.com and solder the ISO7762FDW chips and caps onto them. Needed to isolate UART connection between ODrives and Jetson Nano (to prevent ground loops). Mounted on small custom board (together with IMU).
Jetson Nano 2GB or 4GB | 1 | 78 | 78 | https://eu.robotshop.com/de/products/jetson-nano-dev-expansion-kit-alt-solution-of-b01-kit-w-jetson-io-base-a | https://geizhals.de/nvidia-jetson-nano-developer-kit-a2069594.html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 | Jetson Nano + Wifi USB Adapter. This is already discontinued, so there arn't many sellers. It might be easier to buy it used. The replacement Jetson Nano Orin could theoretically also work, but I haven't tried it.
Wire
Heat Shrink Tubing Set | 1 | 4 | 4 | https://www.amazon.de/-/en/ChiliTec-Heat-Shrink-Tubing-Pieces/dp/B008X4RLJS | https://www.ebay.de/itm/125458914606 | Wire Insulation
40pcs Breadboard Jump Wire F-F 20cm | 1 | 3 | 3
10m Cu wire tinned solid 0.5mm | 2 | 3 | 6 | https://www.ebay.de/itm/391963841090 |  | For custom platines, multiple colors recommended
Silicon Cable Flexibele 30AWG 10m | 1 | 5 | 5 | https://www.ebay.de/itm/133948569165 | https://hobbyking.com/de_de/turnigy-high-quality-30awg-silicone-wire-10m-blue.html | Wire for connecting leg encoders with ODrive. (Needs to be very flexible and low restistance)
USB Cable with 90° plug | 2 | 3 | 6 | https://www.ebay.de/itm/353909457515 |  | Needed to connect stuff to Jetson via USB (ODrive, Mic, Joystick). Cut apart and solder to other Cables as needed.
Micro JST Mini Plugs 2.5mm x 6 | 2 |  | 5 | https://www.ebay.de/itm/183466543983 |  | Connecter to split Leg encoder wire (we just need the plug, desolder the wire and use the silicon wire)
MT60 Amass 3Pin Plug | 4 |  | 11 | https://www.ebay.de/itm/182830571765 |  | Plug to split all BLDC motor wires (Technically these are optional, but without them assembly and disassembly will be very difficult)
Cable Binder | 100 |  | 3
Silicon Cable Flexible 12AWG 2m |  |  | 8 | https://www.ebay.de/itm/315249525208 |  | For battery power distribution to main custom board, and ODrives. Use two colors
XT60 plug | 5 |  | 7 | https://www.ebay.de/itm/183983372460 |  | Plug for connecting both batteries with main custom board and both ODrives (A plug on each of those for easier assembly)
Connector Header | 1 | 9 | 9 | https://www.ebay.de/itm/385427198358 |  | For making cable that connects to the AMS CUI encoders (It's cheaper to assemble them yourself)
UL2547 24AWG Shielded cable 2m 5 Cores | 1 | 5 | 5 | https://www.ebay.de/itm/404104508953 |  | For making cable that connects to the AMS CUI encoders (It's cheaper to assemble them yourself)
Other
3D printer filament 1kg PLA 1.75mm | 1 | 20 | 20 | https://www.ebay.de/itm/264348918066?var=563950433088 |  | Optionally in two colors. Don't buy the cheapest you can find. The cheap ones can get stuck during printing.
Soldering iron set | 1 | 15 | 15 | https://www.ebay.de/itm/394959673405
Multimeter | 1 | 6 | 6 | https://www.ebay.de/itm/126506761449
Jaw / Spider coupling | 1 | 10 | 10 | https://www.ebay.de/itm/115067961451 |  | Pull apart and use each half to fixate the wheel onto the foot motor (The flexible part is not needed). Make sure shaft diameter fits motor axis. The shape can be adjusted in the wheel CAD.
Wireless controller (XBox) | 1 | 20 | 20 | https://www.ebay.de/itm/404311579733 |  | Any wireless controller will do (I use a XBox 360 China clone). But the usb connector must be tiny enough, a long usb stick won't fit! China clones can be tricky to get working on Ubuntu, but possible.
USB Webcam | 1 | 20 | 20 | https://de.aliexpress.com/item/1005004639483886.html |  | Optional, but very helpful for capturing robot movement with the controller application. Should be able to capture at least 60fps
Motor & Encoder
35KG SPT5435LV Digital Servo | 2 | 23 | 46 | https://www.ebay.de/itm/404990246241 |  | Servo for Hip. The China clones are good enough, as long as the internal gears are out of metal. (The cheaper ones are out of plastic)
CUI AMT102-V Encoder | 4 | 25 | 100 | https://www.digikey.de/de/products/detail/cui-devices/AMT102-V/827015 | https://www.mouser.de/ProductDetail/490-AMT102-V | Encoder for hips and feet.
9235-100KV Turnigy Multistar Brushless Multi-Rotor Motor | 2 | 90 | 180 | https://de.aliexpress.com/i/4000563878548.html | https://odriverobotics.com/shop/m8325s | Motors for legs. I bought these on Hobbyking, but they are discontinued. These alternatives look very similar though. (See: https://hobbyking.com/de_de/9235-100kv-turnigy-multistar-brushless-multi-rotor-motor.html)
5055-280kv Turnigy Aerodrive SK3 - Brushless Outrunner Motor | 2 | 55 | 110 | https://hobbyking.com/de_de/turnigy-aerodrive-sk3-5055-430kv-brushless-outrunner-motor.html | https://odriverobotics.com/shop/odrive-custom-motor-d5065 | Motors for feet. This one is discontinued also, but the links point to very similar ones.
AS5048 14-bit Magnetic Rotary Encoder IC | 2 | 20 | 40 | https://www.mouser.de/ProductDetail/ams-OSRAM/AS5048A-TS_EK_AB?qs=Rt6VE0PE%2FOd5D%2Fkw9O7ofA%3D%3D | https://www.digikey.de/de/products/detail/ams-osram-usa-inc/AS5048A-TS-EK-AB/3188612 | Encoder for legs
ODrive 3.6 (2 axis) | 2 | 89 | 178 | https://odriverobotics.com/shop/odrive-v36 | https://de.aliexpress.com/item/1005006656977192.html | Used to control leg and foot motors. It might be possible to get the newer product ODrive S1 to work, but it might be quite some work (also it's not Open Source, it might be impossible). The china clone is cheaper and works (in my experience) just as well.
Battery
Lipo Safe Bag | 1 | 7 | 7 | https://www.ebay.de/itm/192132608682 |  | Battery Storage
XT90S plug | 1 | 6 | 6 | https://www.ebay.de/itm/224453440996
2x 3S Lipo Batteries 11.1V 120C Min 2200mAh | 2 |  | 43 | https://www.ebay.de/itm/143860824357 | https://hobbyking.com/de_de/turnigy-nano-tech-3000mah-3s-30c-lipo-pack-wxt60.html?wrh_pdp=7 | A single larger Lipo battery might also work, but the charger gets more expensive then.
Lipo Charger | 1 | 20 | 20 | https://www.ebay.de/itm/173581616031
Wheel rubber
Color pigments Color powder Inorganic pigments |  |  | 0 | https://www.ebay.de/itm/175176004554 | https://www.ebay.de/itm/183478068028 | Black powder to make rubber wheels black (optional) Coal would probably work also
Kaupo VYTAFLEX 40/1 | 1 | 28 | 28 | https://www.kaupo.de/shop/POLYURETHANKAUTSCHUK/VYTA-FLEX-SERIE/VytaFlex-40/VytaFlex-40-1-Polyurethan.html |  | Used to make the rubber wheels
Vaseline |  |  |  |  |  | Used to isolate the negative forms of the rubber parts
Audio (optional)
Small speaker | 1 | 13 | 13 | https://www.ebay.de/itm/254490551221 |  | If the wires are connected to some plug, just cut the plug off and connect directly to MAX98357 chip
MAX98357A I2S 3W Class D Amplifier Breakout Interface | 1 | 5 | 5 | https://www.ebay.de/itm/314686494101 |  | Chip to control speaker without USB. Is mounted on main custom board. Connected to Jetson via I2S and powered by 5V Converted
USB microphone | 1 | 6 | 6 | https://www.ebay.de/itm/304959862515 |  | You may need to make an USB adapter cable because the USB plug won't fit directly.
Arms (optional)
DFRobot 9G 270DEG METAL SERVO 1.5KG | 6 | 7 | 42 | https://www.digikey.de/de/products/detail/dfrobot/SER0046/11613083 | https://www.ebay.de/itm/164790150432 | Small servos for arms (China clones arn't much cheaper and much worse quality, also need slightliy adjusted CAD)
Cylindrical screws DIN 912 A2 V2A M2.5 10mm | 10 |  | 3 | https://www.ebay.de/itm/123990393323
Cylindrical screws DIN 912 A2 V2A M2.5 6mm | 100 |  | 5 | https://www.ebay.de/itm/123990393323
TOTAL |  |  | 1188 | EUR

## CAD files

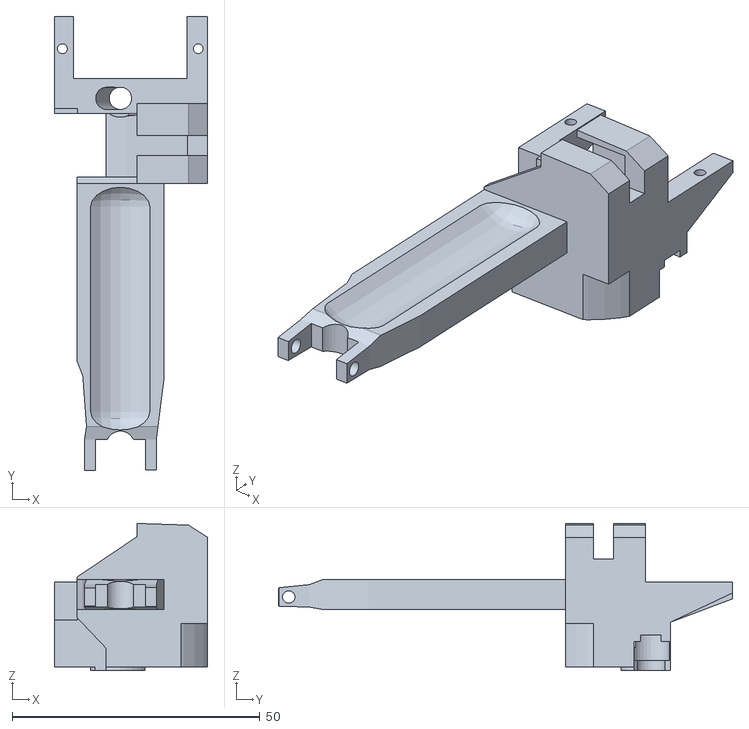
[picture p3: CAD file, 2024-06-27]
CAD/Meshes/arm_mirror/upper_arm.stl
30.9 x 91.6 x 29.7

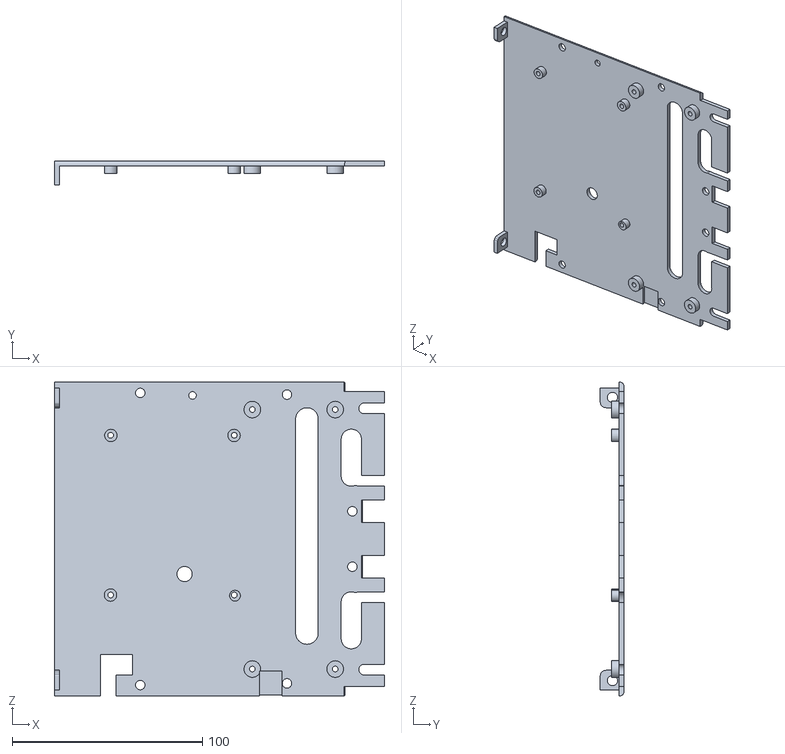
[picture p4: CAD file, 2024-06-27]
CAD/Meshes/body/body_back.stl
173.5 x 12.5 x 165.0

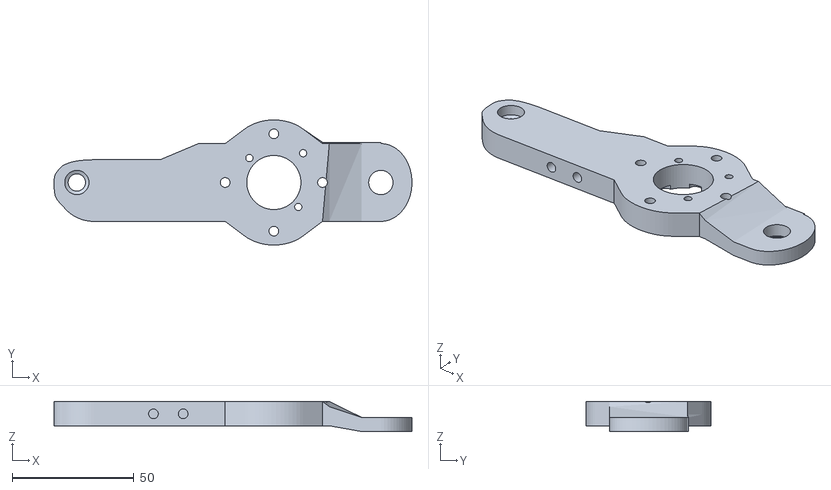
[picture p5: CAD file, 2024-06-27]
CAD/Meshes/leg_mirror/upper_leg_center.stl
147.2 x 51.4 x 12.4

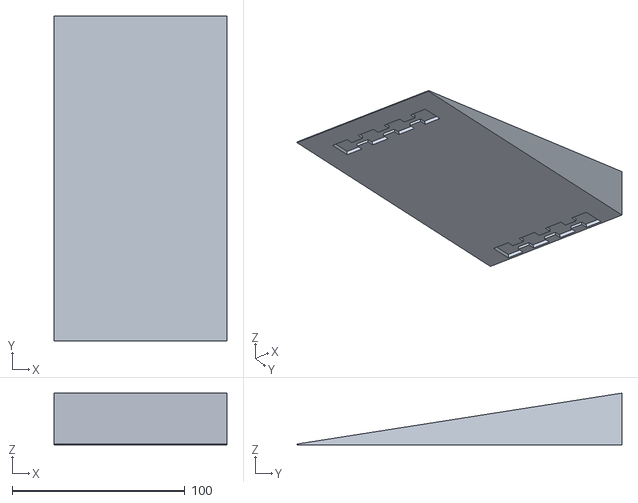
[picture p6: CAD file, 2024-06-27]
CAD/Meshes/small_ramp.stl
100.0 x 188.2 x 30.0

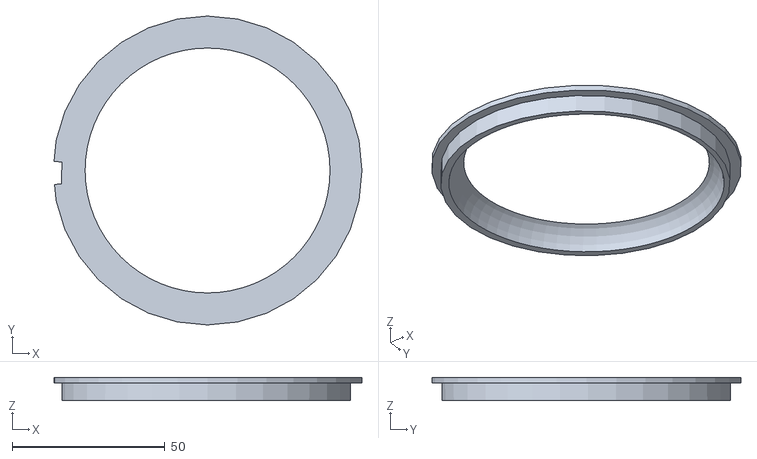
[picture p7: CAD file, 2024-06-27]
CAD/Meshes/wheel_double/wheel_rubber_negative_form_3.stl
100.9 x 101.2 x 7.64

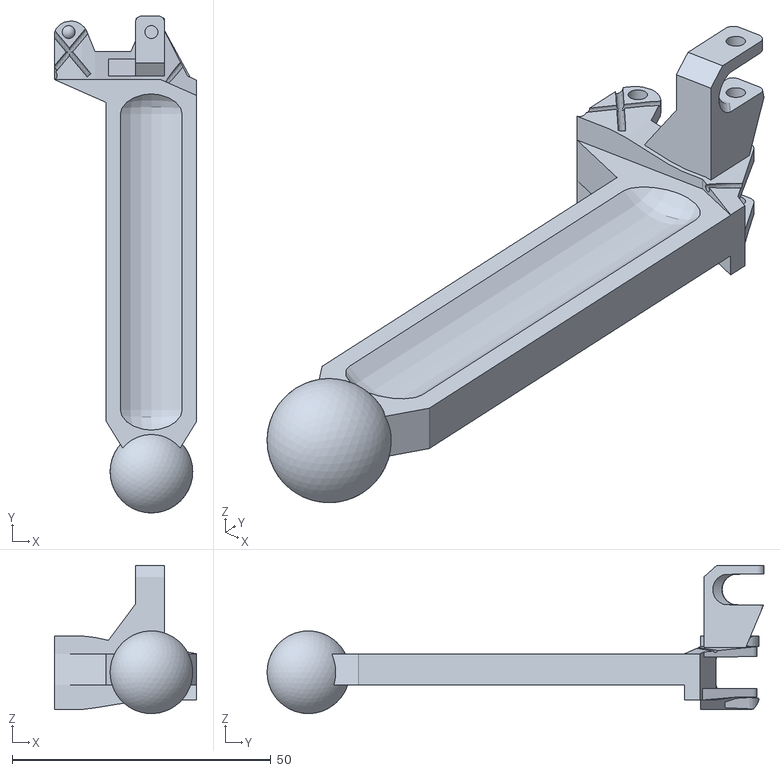
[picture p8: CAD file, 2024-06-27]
CAD/Meshes/arm_mirror/lower_arm.stl
27.5 x 96.1 x 28.7

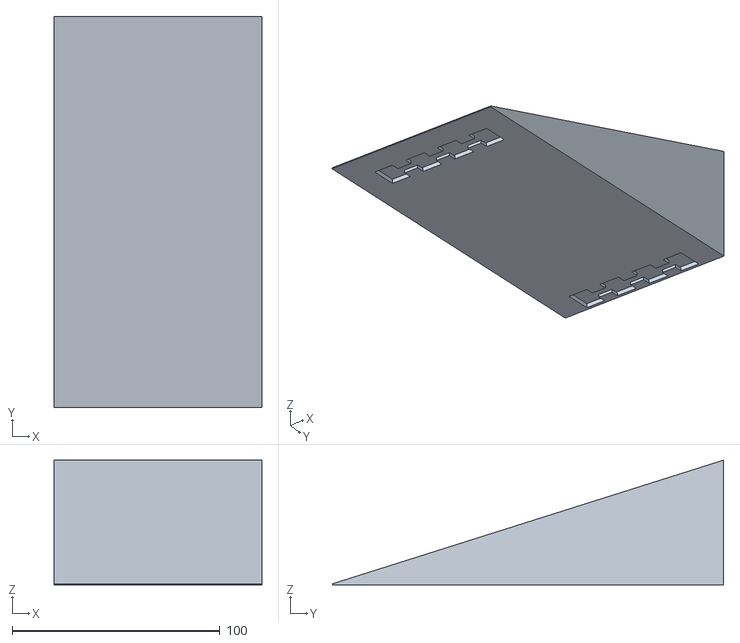
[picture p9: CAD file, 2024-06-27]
CAD/Meshes/big_ramp.stl
100.0 x 188.2 x 60.0

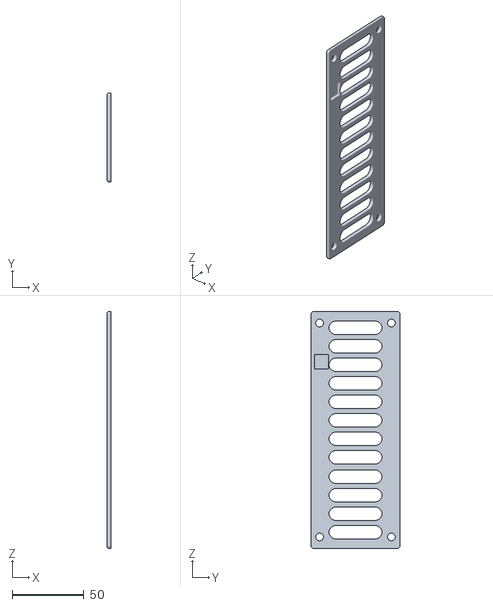
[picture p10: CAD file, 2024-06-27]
CAD/Meshes/body/body_top.stl
2.50 x 62.0 x 165.0

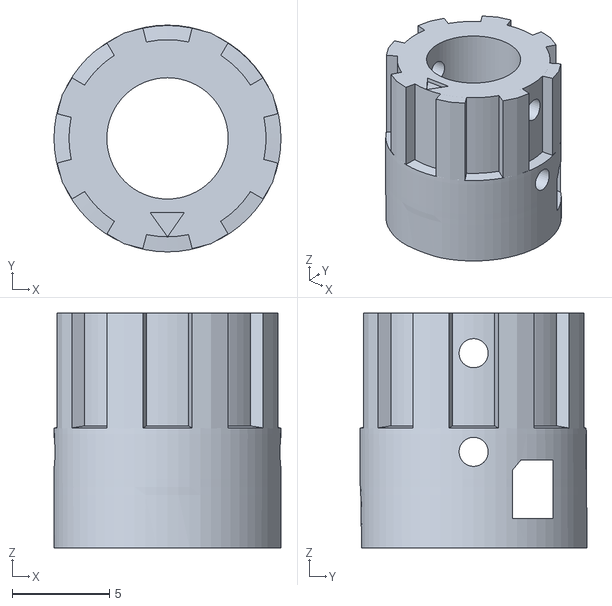
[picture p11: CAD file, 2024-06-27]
CAD/Meshes/leg_mirror/foot_encoder_adapter_1.stl
11.7 x 11.7 x 12.1

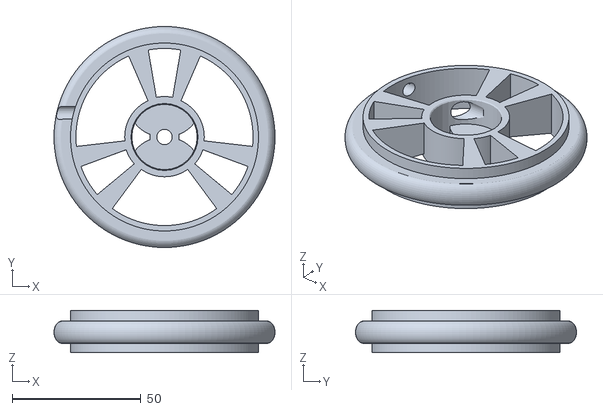
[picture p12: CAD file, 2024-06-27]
CAD/Meshes/wheel_double/wheel.stl
85.8 x 85.8 x 16.5

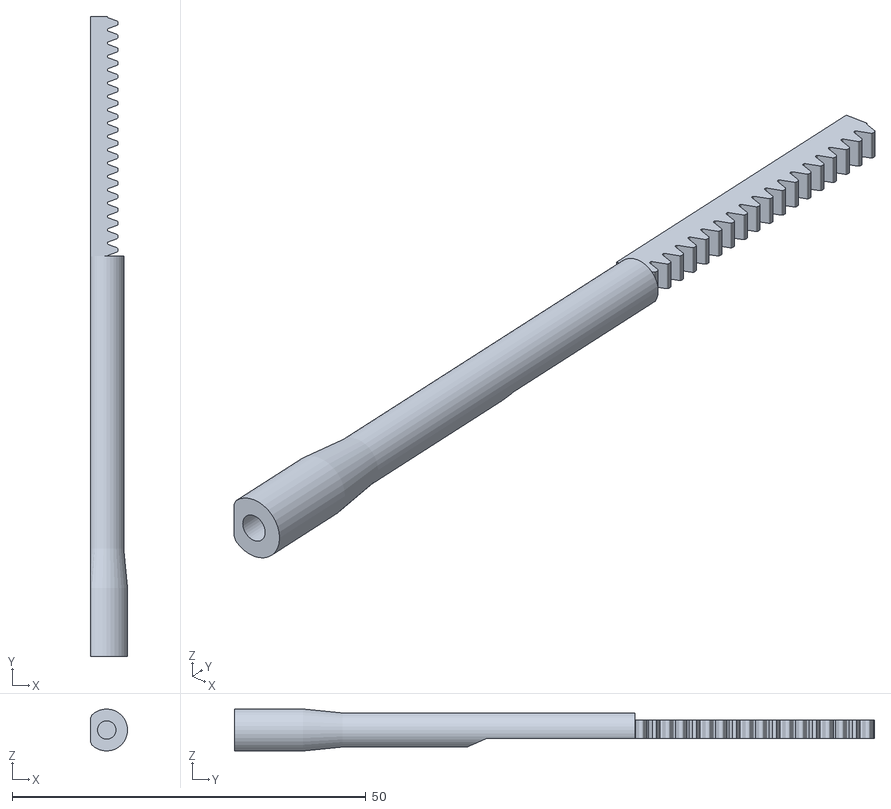
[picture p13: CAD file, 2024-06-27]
CAD/Meshes/arm_mirror/upper_arm_slider_b_1.stl
5.26 x 90.4 x 5.93

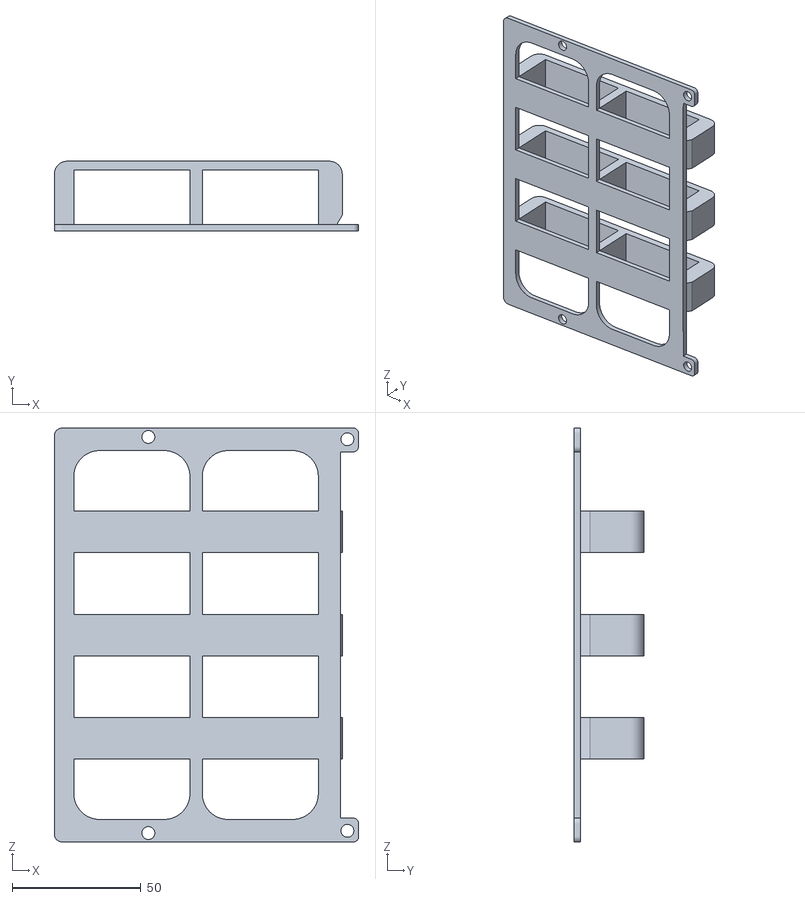
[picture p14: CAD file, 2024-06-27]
CAD/Meshes/battery_holder.stl
118.0 x 27.0 x 160.5

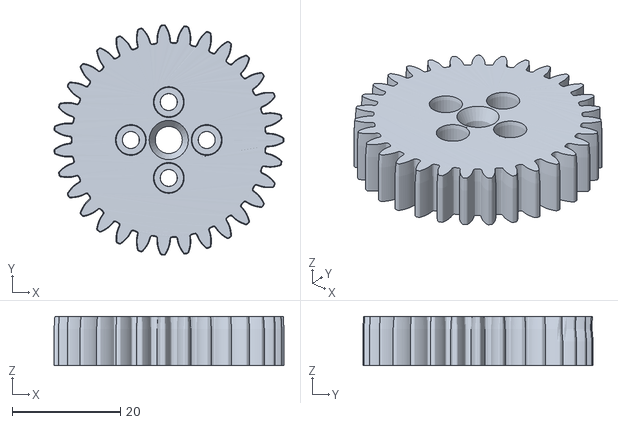
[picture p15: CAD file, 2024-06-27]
CAD/Meshes/body/hip_gear_double.stl
42.5 x 42.6 x 9.14

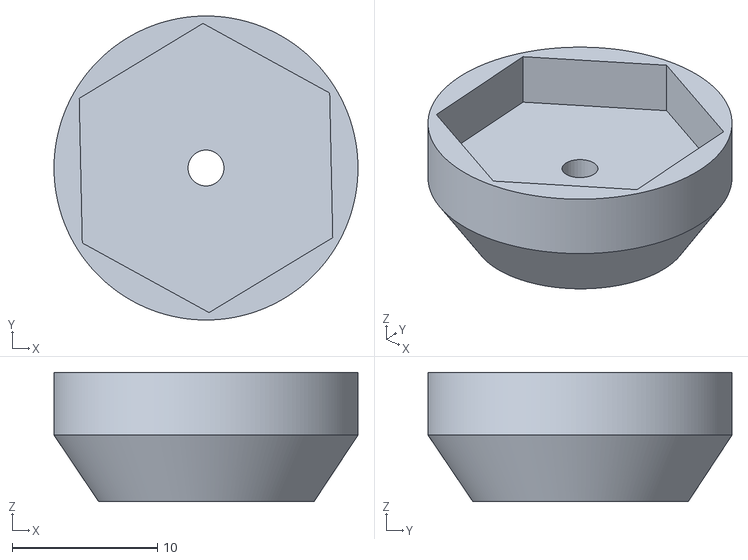
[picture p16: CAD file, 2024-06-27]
CAD/Meshes/leg_mirror/leg_magnet_holder.stl
20.9 x 20.9 x 8.90

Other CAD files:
CAD/Meshes/wheel_double/wheel_rubber_negative_form_1.stl
CAD/Meshes/arm_mirror/arm_rubber_negative.stl
CAD/Meshes/body/body_side_mirror.stl
CAD/Meshes/leg_mirror/upper_leg_side.stl
CAD/FootEncoderAdapter.blend
CAD/Meshes/arm_mirror/arm_joint_connector_c.stl
CAD/Meshes/arm_mirror/arm_joint_connector_double.stl
CAD/Meshes/arm_mirror/upper_arm_gear_double.stl
CAD/Meshes/arm_mirror/upper_arm_gear_holder_double.stl
CAD/Meshes/arm_mirror/upper_arm_handle_holder.stl
CAD/Meshes/arm_mirror/upper_arm_slider_b_2.stl
CAD/Meshes/arm_mirror/upper_arm_slider_c.stl
CAD/Meshes/body/body_bottom.stl
CAD/Meshes/body/body_front.stl
CAD/Meshes/leg_mirror/foot_encoder_adapter_2.stl
CAD/Meshes/leg_mirror/leg_gear.stl
CAD/Meshes/leg_mirror/lower_leg_center.stl
CAD/Meshes/leg_mirror/lower_leg_side.stl
CAD/Meshes/leg_mirror/upper_leg_encoder_cover.stl
CAD/Meshes/leg_mirror/upper_leg_stabilisator.stl
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

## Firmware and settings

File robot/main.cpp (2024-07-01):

// Main program that is run on the Jetson Nano inside the robot.

#ifdef COMPILING_CONTROL_UI
#error COMPILING_CONTROL_UI must not be defined for the robot project
#endif

#include <cstdlib>
#include <stdio.h>
#include <sys/param.h>
#include <sys/resource.h>
#include <time.h>
#include <algorithm>
#include "main.h"
#include "server.h"
#include "leg_control.h"
#include "foot_control.h"
#include "battery.h"
#include "servo.h"
#include "balance_control.h"
#include "joystick.h"
#include "imu/spi_imu.h"
#include "body_acc.h"
#include "../common/leaning.h"
#include "../common/time_helper.h"
#include "ik.h"
#include "statistics.h"
#include "tts_client.h"
#include "asr_client.h"
#include "command.h"

bool running = true;
MonitorData md;
ControlData cd;

static void ctrl_c_handler(int signum)
{
	running = false;
}

static void setup_handlers()
{
	struct sigaction sa = { 0 };
	sa.sa_handler = ctrl_c_handler;

	// If we don't set SA_RESTART, the recv call to the uart file handle in ODrive will fail.
	sa.sa_flags = SA_RESTART | SA_NOCLDSTOP;

	sigaction(SIGINT, &sa, NULL);
	sigaction(SIGTERM, &sa, NULL);
}

bool init_i2c()
{
	FILE* file = fopen("/sys/bus/i2c/devices/i2c-1/bus_clk_rate", "w");
	if (!file)
	{
		perror("init_i2c");
		return false;
	}
    fprintf(file, "400000\n");
	fclose(file);
	return true;
}

int main(int argc, char *argv[])
{
	int result = EXIT_FAILURE;
	u32_micros last_time;
	setup_handlers();

	// Set higher priority to own process.
    if (setpriority(PRIO_PROCESS, 0, -20) != 0)
		printf("cannot set priority\n");
	
	//u64 start_time2 = time_micros_64();
	
	if (!joystick_init())       goto fail;
	if (!init_i2c())            goto fail;
	if (!leg_control_init())
	{
		battery_init();
		goto fail;
	}
	if (!battery_init())        goto fail;
	if (!tts_client_init())     goto fail;
	if (!foot_control_init())   goto fail;
	leg_control_init2();
	if (!balance_control_init())goto fail;
	if (!servo_motors_init())   goto fail;
	if (!body_acc_init())       goto fail;
	if (!leaning_init())        goto fail;
	if (!ik_init())             goto fail;
	if (!spi_imu_init())        goto fail;
	if (!server_init())         goto fail;
	if (!asr_client_init())     goto fail;
	if (!command_init())        goto fail;
	
	last_time = time_micros();
	md.delta_time = 0.004f;
	
	while (running)
	{
		if (!joystick_update())       goto fail;
		if (!battery_update())        goto fail;
		if (!body_acc_update())       goto fail;
		if (!leaning_update())        goto fail;
		if (!ik_update())             goto fail;
		if (!spi_imu_update())        goto fail;
		if (!leg_control_update())    goto fail;
		if (!foot_control_update_1()) goto fail;
		if (!balance_control_update())goto fail;
		if (!foot_control_update_2()) goto fail;
		if (!servo_motors_update())   goto fail;
		if (!statistics_update())     goto fail;
		if (!server_update())         goto fail;
		if (!tts_client_update())     goto fail;
		if (!asr_client_update())     goto fail;
		if (!command_update())        goto fail;
		
		// calculate delta time

		u32_micros start_time = time_micros();
		if (cd.target_delta_time_ms == 0)
			precise_sleep(0.001);
		else
		{
			double target_delta = cd.target_delta_time_ms * 0.001;
			double delta = double(start_time - last_time) * .000001;
			double remaining = target_delta - delta;
			precise_sleep(remaining);
		}

		static int last_pause_trigger;
		if (cd.pause_trigger-last_pause_trigger == 1)
			precise_sleep(cd.pause_delta_time_ms * 0.001);
		last_pause_trigger = cd.pause_trigger;

		if (cd.do_random_pauses)
			precise_sleep((rand()%cd.random_pauses_max_ms) * 0.001);

		u32_micros current_time = time_micros();
		md.delta_time_sleep = current_time - start_time;

		md.delta_time_micros = current_time - last_time;
		last_time = current_time;
		md.delta_time = float(md.delta_time_micros) * .000001f;

		md.uptime_jetson_micros = time_micros_64();
		time(&md.local_time);

		md.counter++;
	}
	printf("\n");
	result = EXIT_SUCCESS;
fail:
	//if (result == EXIT_FAILURE)
	//	tts_say_text("Something failed. Shutting down.");
	server_close();
	spi_imu_close();
	body_acc_close();
	leaning_close();
	ik_close();
	servo_motors_close();
	balance_control_close();
	battery_close();
	foot_control_close();
	leg_control_close();
	joystick_close();
	tts_client_close();
	asr_client_close();
	command_close();
	return result;
}

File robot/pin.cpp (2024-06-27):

#include "pin.h"
#include <stdio.h>
#include <algorithm>
//#include <pigpio.h>
#include <assert.h>


#include <stdio.h>
#include <stdlib.h>
#include <string.h>
#include <errno.h>
#include <unistd.h>
#include <fcntl.h>
#include <poll.h>

int exported_pins[64];
int num_exported_pins = 0;

#define SYSFS_GPIO_DIR "/sys/class/gpio"
//#define POLL_TIMEOUT (3 * 1000) /* 3 seconds */
#define MAX_BUF 64

#ifndef _MSC_VER
#pragma GCC diagnostic ignored "-Wunused-result"
#endif


// source: JETSON_NANO_PIN_DEFS in gpio_pin_data.py in https://github.com/NVIDIA/jetson-gpio.git
struct JetsonMapping
{
	int jetson;
	int pin;
	int pi;
};
JetsonMapping jetson_mapping[] = {
    {216, 7 , 4 },
    {50 , 11, 17},
    {79 , 12, 18},
    {14 , 13, 27},
    {194, 15, 22},
    {232, 16, 23},
    {15 , 18, 24},
    {16 , 19, 10},
    {17 , 21, 9 },
    {13 , 22, 25},
    {18 , 23, 11},
    {19 , 24, 8 },
    {20 , 26, 7 },
    {149, 29, 5 },
    {200, 31, 6 },
    {168, 32, 12},
    {38 , 33, 13},
    {76 , 35, 19},
    {51 , 36, 16},
    {12 , 37, 26},
    {77 , 38, 20},
    {78 , 40, 21},
};
int pi_to_jetson[30];


bool pin_init()
{
	//if (gpioInitialise()<0) return 1;
	for (int i = 0; i < sizeof(jetson_mapping) / sizeof(jetson_mapping[0]); i++)
	{
		pi_to_jetson[jetson_mapping[i].pi] = jetson_mapping[i].jetson;
	}
	return true;
}

int pin_unexport(unsigned int gpio)
{
	int fd, len;
	char buf[MAX_BUF];
 
	//printf("unexport %d\n", gpio);

	fd = open(SYSFS_GPIO_DIR "/unexport", O_WRONLY);
	if (fd < 0) {
		printf("unexport %d failed!\n", gpio);
		//perror("gpio/export");
		return fd;
	}
 
	len = snprintf(buf, sizeof(buf), "%d", gpio);
	int r = write(fd, buf, len);
	//assert(r == len);
	close(fd);
	return 0;
}

void pin_close()
{
	//gpioTerminate();
	/*for (int i = 0; i < num_exported_pins; i++)
		pin_unexport(exported_pins[i]);
	num_exported_pins = 0;*/
}




 /****************************************************************
 * Constants
 ****************************************************************/
 

bool pin_export(unsigned int gpio)
{
	int fd, len;
	char buf[MAX_BUF];

	//printf("export %d\n", gpio);

	fd = open(SYSFS_GPIO_DIR "/export", O_WRONLY);
	if (fd < 0) {
		perror("gpio/export");
		return false;
	}
 
	len = snprintf(buf, sizeof(buf), "%d", gpio);
	int r = write(fd, buf, len);
	if (r < 0)
		printf("err %s\n", strerror(errno));
	assert(r == len);
	close(fd);
	if (r >= 0)
	{
		if (num_exported_pins < 64)
			exported_pins[num_exported_pins++] = gpio;
		else
			assert(0);
	}
	return r >= 0;
}


/****************************************************************
 * gpio_set_dir
 ****************************************************************/
bool pin_set_mode(unsigned int pin, PinMode mode)
{
	int fd, len;
	char buf[MAX_BUF];

	int gpio = pi_to_jetson[pin];
	assert(gpio);
	pin_unexport(gpio);
	pin_export(gpio);

	//printf("set_mode %d\n", gpio);
 
	len = snprintf(buf, sizeof(buf), SYSFS_GPIO_DIR  "/gpio%d/direction", gpio);
 
	fd = open(buf, O_WRONLY);
	if (fd < 0)
	{
		perror("pin_set_mode");
		return false;
	}
 
	if (mode == pin_mode_out)
	{
		int r = write(fd, "out", 4);
		assert(r == 4);
	}
	else
	{
		int r = write(fd, "in", 3);
		assert(r == 3);
	}
 
	close(fd);
	return true;
}

/****************************************************************
 * gpio_set_value
 ****************************************************************/
bool pin_set(unsigned int pin, unsigned int value)
{
	int fd, len;
	char buf[MAX_BUF];

	int gpio = pi_to_jetson[pin];
 
	len = snprintf(buf, sizeof(buf), SYSFS_GPIO_DIR "/gpio%d/value", gpio);
 
	fd = open(buf, O_WRONLY);
	if (fd < 0) {
		perror("gpio/set-value");
		return false;
	}
 
	int r = write(fd, value ? "1" : "0", 2);
	if (r < 0)
		printf("pin_set %s\n", strerror(errno));
 
	close(fd);
	return true;
}

/****************************************************************
 * gpio_get_value
 ****************************************************************/
int gpio_get_value(unsigned int gpio, unsigned int *value)
{
	int fd, len;
	char buf[MAX_BUF];
	char ch;

	len = snprintf(buf, sizeof(buf), SYSFS_GPIO_DIR "/gpio%d/value", gpio);
 
	fd = open(buf, O_RDONLY);
	if (fd < 0) {
		perror("gpio/get-value");
		return fd;
	}
 
	read(fd, &ch, 1);

	if (ch != '0') {
		*value = 1;
	} else {
		*value = 0;
	}
 
	close(fd);
	return 0;
}


/****************************************************************
 * gpio_set_edge
 ****************************************************************/

int gpio_set_edge(unsigned int gpio, char *edge)
{
	int fd, len;
	char buf[MAX_BUF];

	len = snprintf(buf, sizeof(buf), SYSFS_GPIO_DIR "/gpio%d/edge", gpio);
 
	fd = open(buf, O_WRONLY);
	if (fd < 0) {
		perror("gpio/set-edge");
		return fd;
	}
 
	write(fd, edge, strlen(edge) + 1); 
	close(fd);
	return 0;
}

/****************************************************************
 * gpio_fd_open
 ****************************************************************/

int gpio_fd_open(unsigned int gpio)
{
	int fd, len;
	char buf[MAX_BUF];

	len = snprintf(buf, sizeof(buf), SYSFS_GPIO_DIR "/gpio%d/value", gpio);
 
	fd = open(buf, O_RDONLY | O_NONBLOCK );
	if (fd < 0) {
		perror("gpio/fd_open");
	}
	return fd;
}

/****************************************************************
 * gpio_fd_close
 ****************************************************************/

int gpio_fd_close(int fd)
{
	return close(fd);
}

/****************************************************************
 * Main
 ****************************************************************/
/*int main(int argc, char **argv, char **envp)
{
	struct pollfd fdset[2];
	int nfds = 2;
	int gpio_fd, timeout, rc;
	char *buf[MAX_BUF];
	unsigned int gpio;
	int len;



	if (argc < 2) {
		printf("Usage: gpio-int <gpio-pin>\n\n");
		printf("Waits for a change in the GPIO pin voltage level or input on stdin\n");
		exit(-1);
	}

	gpio = atoi(argv[1]);

	gpio_export(gpio);
	gpio_set_dir(gpio, 0);
	gpio_set_edge(gpio, "rising");
	gpio_fd = gpio_fd_open(gpio);

	timeout = POLL_TIMEOUT;
 
	while (1) {
		memset((void*)fdset, 0, sizeof(fdset));

		fdset[0].fd = STDIN_FILENO;
		fdset[0].events = POLLIN;
      
		fdset[1].fd = gpio_fd;
		fdset[1].events = POLLPRI;

		rc = poll(fdset, nfds, timeout);      

		if (rc < 0) {
			printf("\npoll() failed!\n");
			return -1;
		}
      
		if (rc == 0) {
			printf(".");
		}
            
		if (fdset[1].revents & POLLPRI) {
			lseek(fdset[1].fd, 0, SEEK_SET);
			len = read(fdset[1].fd, buf, MAX_BUF);
			printf("\npoll() GPIO %d interrupt occurred\n", gpio);
		}

		if (fdset[0].revents & POLLIN) {
			(void)read(fdset[0].fd, buf, 1);
			printf("\npoll() stdin read 0x%2.2X\n", (unsigned int) buf[0]);
		}

		fflush(stdout);
	}

	gpio_fd_close(gpio_fd);
	return 0;
}*/

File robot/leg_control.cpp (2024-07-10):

// This handles communication with the ODrive that is connected to the big motors on the legs.
// That is the ODrive that is placed on the front (the side with no batteries) and connected
// to the Jetson via /dev/ttyTHS1 (on the 40-Pin Header).
//
// This ODrive is connected to the leg motors, its sensors (AS5048 Magnetic Rotary Absolute Encoders),
// and also to the CUI AMT Encoders on the hips. This ODrive doesn't really have anything to do with the
// hip, but the Jetson cannot directly communicate with these encoders. So we abuse this ODrive for reading
// the hip encoders because it has free ports for it and it doesn't cost much CPU time. (We need to use
// a custom built firmware for this though).
// 
// Apart from that sensor reading, the code in this file is mainly responsible for these features:
//  - Controlling the leg motors in position control.
//  - Jumping
//  - Side Balancing
//  - Retrieving ODrive oscilloscope data
// 
// Jumping
// The code for jumping has gotten surprisingly complex. A jump is separated into different phases
// (see the enum JumpPhase) and each phase triggers different code. Most of that code is here, but some
// of it is also in the custom ODrive firmware, and also in other modules
// (servo, foot_control, IMU, balance control). The jump itself may not be so complicated, but landing and
// not falling over after a jump turned out to be a quite complex task, and simply requires modifications in
// all those other modules.
//
// Side Balancing
// What's that? That's a name I made up for the mode, where the robot tries to stand straight (no leaning
// to left or right), regardless of what the ground looks like. It's not enabled by default and is used
// for example when the robot drives with one wheel over a ramp. In this mode, the imu side angle is used
// to control the leg motors in such a way, that the side angle is close to zero. Unfortunately, I've never
// gotten this mode to be very stable, that's why it must be enabled explicitly in control_ui.
// The problem is that the actuator of this controller, the changing of the difference of effective leg
// height on each side, doesn't necessarily affect the measured imu side angle directly. It's possible that
// one leg gets airborne, and there is no sensor to detect that. Even if not, it's hard to predict the behavior
// of the whole robot in this scenario. There is also very little leeway. Once the side angle gets so large
// that the center of mass gets over the corresponding wheel, there is nothing the controller can do to
// lean the robot back. Another issue is that in order to handle ramps, to controller needs to be very fast.
// It's implementation is also partly in the ODrive firmware, because the control loop in the robot is
// too slow for it.
//
// Oscilloscope data
// You can also access ODrive oscilloscope data here. That is data that is recorded on ODrive in 8kHz
// and can be used to debug control loop issues. That data can be displayed inline in the plots in control_ui.
// It's very useful to debug issues with both jumping and sidebalancing, especially in combination with
// a video stream.
// 
// Axis numbers are: left = 1, right = 0 (This way the motor wires don't have to cross)

#include "leg_control.h"
#include "../common/odrive/odrive_helper.h"
#include "main.h"
#include "tts_client.h"

#include <string>
#include <math.h>

static void leg_control_update_axis(Endpoint* axis, int leg, float delta_time_unclamped);

ODrive odrive;
static Endpoint* axis0;
static Endpoint* axis1;

static int cd_counter;
static bool motor_running[2];

int oscilloscope_size = 0;

int odrive_enable_side_balance;

bool calibration_leg_done[2];
float calibration_leg_pos[2];
float calibration_leg_rel_pos_max[2];

bool zombie_mode = false;
float zombie_mode_timer;

inline uint as_uint(const float x) {
    union { float f; uint i; } val;
    val.f = x;
    return val.i;
}
inline float as_float(const uint x) {
    union { float f; uint i; } val;
    val.i = x;
    return val.f;
}

float half_to_float(ushort x) { // IEEE-754 16-bit floating-point format (without infinity): 1-5-10, exp-15, +-131008.0, +-6.1035156E-5, +-5.9604645E-8, 3.311 digits
    const uint e = (x&0x7C00)>>10; // exponent
    const uint m = (x&0x03FF)<<13; // mantissa
    const uint v = as_uint((float)m)>>23; // evil log2 bit hack to count leading zeros in denormalized format
    return as_float((x&0x8000)<<16 | (e!=0)*((e+112)<<23|m) | ((e==0)&(m!=0))*((v-37)<<23|((m<<(150-v))&0x007FE000))); // sign : normalized : denormalized
}

static bool check_errors(Endpoint& root, bool init)
{
	if (odrive.communication_error)
	{
		printf("ODrive Leg communication error\n");
		return false;
	}

	int num_errors = 0;

	if (md.startup_sequence != SS_LegCalibration1a && md.startup_sequence != SS_LegCalibration1b &&
		(motor_running[0] || motor_running[1]))
	{
		float abs_pos0 = -(md.leg_rel_angle[0]+md.leg_base_angle[0]);
		float abs_pos1 =  (md.leg_rel_angle[1]+md.leg_base_angle[1]);
		if (abs_pos0 > 1.2f || abs_pos1 > 1.2f ||
			abs_pos0 < -0.75f || abs_pos1 < -0.75f)
		{
			// It is physically impossible to reach these positions
			// so if it happens an encoder is probably defect and we fail here.
			printf("ODrive Leg position out of range: %f %f\n", abs_pos0, abs_pos1);
			num_errors++;
		}
	}

	if (zombie_mode)
	{
		zombie_mode_timer -= md.delta_time;
		if (zombie_mode_timer <= 0)
			return false;
		return true;
	}

	bool any_errors = true;
	root("any_errors_and_watchdog_feed").get(any_errors);
	if (!any_errors && num_errors == 0)
		return true;
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

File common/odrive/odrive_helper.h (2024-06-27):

// This has some helper functions and constants that come in handy when dealing with ODrive
// but it's all optional.
// The constants are copied from the ODrive repo and are needed because they are not part
// of the ODrive json definition file.
#pragma once
#include "ODrive.h"
#include "endpoint.h"

const int AXIS_STATE_UNDEFINED = 0;           //<! will fall through to idle
const int AXIS_STATE_IDLE = 1;                //<! disable PWM and do nothing
const int AXIS_STATE_STARTUP_SEQUENCE = 2; //<! the actual sequence is defined by the config.startup_... flags
const int AXIS_STATE_FULL_CALIBRATION_SEQUENCE = 3;   //<! run all calibration procedures; then idle
const int AXIS_STATE_MOTOR_CALIBRATION = 4;   //<! run motor calibration
const int AXIS_STATE_SENSORLESS_CONTROL = 5;  //<! run sensorless control
const int AXIS_STATE_ENCODER_INDEX_SEARCH = 6; //<! run encoder index search
const int AXIS_STATE_ENCODER_OFFSET_CALIBRATION = 7; //<! run encoder offset calibration
const int AXIS_STATE_CLOSED_LOOP_CONTROL = 8;  //<! run closed loop control
const int AXIS_STATE_LOCKIN_SPIN                   = 9;
const int AXIS_STATE_ENCODER_DIR_FIND              = 10;
const int AXIS_STATE_HOMING                        = 11;
const int AXIS_STATE_ENCODER_HALL_POLARITY_CALIBRATION = 12;
const int AXIS_STATE_ENCODER_HALL_PHASE_CALIBRATION = 13;

// from: ODrive/Firmware/autogen/interfaces.hpp
// also here: ODrive/tools/odrive/enums.py
const int AXIS_ERROR_INVALID_STATE               = 0x00000001;
const int AXIS_ERROR_DC_BUS_UNDER_VOLTAGE        = 0x00000002;
const int AXIS_ERROR_DC_BUS_OVER_VOLTAGE         = 0x00000004;
const int AXIS_ERROR_CURRENT_MEASUREMENT_TIMEOUT = 0x00000008;
const int AXIS_ERROR_BRAKE_RESISTOR_DISARMED     = 0x00000010;
const int AXIS_ERROR_MOTOR_DISARMED              = 0x00000020;
const int AXIS_ERROR_MOTOR_FAILED                = 0x00000040;
const int AXIS_ERROR_SENSORLESS_ESTIMATOR_FAILED = 0x00000080;
const int AXIS_ERROR_ENCODER_FAILED              = 0x00000100;
const int AXIS_ERROR_CONTROLLER_FAILED           = 0x00000200;
const int AXIS_ERROR_POS_CTRL_DURING_SENSORLESS  = 0x00000400;
const int AXIS_ERROR_WATCHDOG_TIMER_EXPIRED      = 0x00000800;
const int AXIS_ERROR_MIN_ENDSTOP_PRESSED         = 0x00001000;
const int AXIS_ERROR_MAX_ENDSTOP_PRESSED         = 0x00002000;
const int AXIS_ERROR_ESTOP_REQUESTED             = 0x00004000;
const int AXIS_ERROR_HOMING_WITHOUT_ENDSTOP      = 0x00020000;
const int AXIS_ERROR_OVER_TEMP                   = 0x00040000;
const int AXIS_ERROR_UNKNOWN_POSITION            = 0x00080000;

const s64 MOTOR_ERROR_PHASE_RESISTANCE_OUT_OF_RANGE   = 0x000000001;
const s64 MOTOR_ERROR_PHASE_INDUCTANCE_OUT_OF_RANGE   = 0x000000002;
const s64 MOTOR_ERROR_ADC_FAILED                      = 0x000000004;
const s64 MOTOR_ERROR_DRV_FAULT                       = 0x000000008;
const s64 MOTOR_ERROR_CONTROL_DEADLINE_MISSED         = 0x000000010;
const s64 MOTOR_ERROR_NOT_IMPLEMENTED_MOTOR_TYPE      = 0x000000020;
const s64 MOTOR_ERROR_BRAKE_CURRENT_OUT_OF_RANGE      = 0x000000040;
const s64 MOTOR_ERROR_MODULATION_MAGNITUDE            = 0x000000080;
const s64 MOTOR_ERROR_BRAKE_DEADTIME_VIOLATION        = 0x000000100;
const s64 MOTOR_ERROR_UNEXPECTED_TIMER_CALLBACK       = 0x000000200;
const s64 MOTOR_ERROR_CURRENT_SENSE_SATURATION        = 0x000000400;
const s64 MOTOR_ERROR_CURRENT_LIMIT_VIOLATION         = 0x000001000;
const s64 MOTOR_ERROR_BRAKE_DUTY_CYCLE_NAN            = 0x000002000;
const s64 MOTOR_ERROR_DC_BUS_OVER_REGEN_CURRENT       = 0x000004000;
const s64 MOTOR_ERROR_DC_BUS_OVER_CURRENT             = 0x000008000;
const s64 MOTOR_ERROR_MODULATION_IS_NAN               = 0x000010000;
const s64 MOTOR_ERROR_MOTOR_THERMISTOR_OVER_TEMP      = 0x000020000;
const s64 MOTOR_ERROR_FET_THERMISTOR_OVER_TEMP        = 0x000040000;
const s64 MOTOR_ERROR_TIMER_UPDATE_MISSED             = 0x000080000;
const s64 MOTOR_ERROR_CURRENT_MEASUREMENT_UNAVAILABLE = 0x000100000;
const s64 MOTOR_ERROR_CONTROLLER_FAILED               = 0x000200000;
const s64 MOTOR_ERROR_I_BUS_OUT_OF_RANGE              = 0x000400000;
const s64 MOTOR_ERROR_BRAKE_RESISTOR_DISARMED         = 0x000800000;
const s64 MOTOR_ERROR_SYSTEM_LEVEL                    = 0x001000000;
const s64 MOTOR_ERROR_BAD_TIMING                      = 0x002000000;
const s64 MOTOR_ERROR_UNKNOWN_PHASE_ESTIMATE          = 0x004000000;
const s64 MOTOR_ERROR_UNKNOWN_PHASE_VEL               = 0x008000000;
const s64 MOTOR_ERROR_UNKNOWN_TORQUE                  = 0x010000000;
const s64 MOTOR_ERROR_UNKNOWN_CURRENT_COMMAND         = 0x020000000;
const s64 MOTOR_ERROR_UNKNOWN_CURRENT_MEASUREMENT     = 0x040000000;
const s64 MOTOR_ERROR_UNKNOWN_VBUS_VOLTAGE            = 0x080000000;
const s64 MOTOR_ERROR_UNKNOWN_VOLTAGE_COMMAND         = 0x100000000;
const s64 MOTOR_ERROR_UNKNOWN_GAINS                   = 0x200000000;
const s64 MOTOR_ERROR_CONTROLLER_INITIALIZING         = 0x400000000;
const s64 MOTOR_ERROR_UNBALANCED_PHASES               = 0x800000000;


const int ENCODER_MODE_INCREMENTAL                 = 0;
const int ENCODER_MODE_HALL                        = 1;
const int ENCODER_MODE_SINCOS                      = 2;
const int ENCODER_MODE_SPI_ABS_CUI                 = 256;
const int ENCODER_MODE_SPI_ABS_AMS                 = 257;
const int ENCODER_MODE_SPI_ABS_AEAT                = 258;
const int ENCODER_MODE_SPI_ABS_RLS                 = 259;
const int ENCODER_MODE_SPI_ABS_MA732               = 260;

const int CONTROL_MODE_VOLTAGE_CONTROL  = 0;
const int CONTROL_MODE_TORQUE_CONTROL   = 1;
const int CONTROL_MODE_VELOCITY_CONTROL = 2;
const int CONTROL_MODE_POSITION_CONTROL = 3;

const int INPUT_MODE_INACTIVE                      = 0;
const int INPUT_MODE_PASSTHROUGH                   = 1;
const int INPUT_MODE_VEL_RAMP                      = 2;
const int INPUT_MODE_POS_FILTER                    = 3;
const int INPUT_MODE_MIX_CHANNELS                  = 4;
const int INPUT_MODE_TRAP_TRAJ                     = 5;
const int INPUT_MODE_TORQUE_RAMP                   = 6;
const int INPUT_MODE_MIRROR                        = 7;
const int INPUT_MODE_TUNING                        = 8;
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

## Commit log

2024-06-27 Commit robot related stuff into separate repo (Original repo is too large for Github)
    [FootEncoderAdapter.blend, Ramp.blend, Wheel.blend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]
2024-06-29 Add CAD readme
2024-06-30 Add llm and ODrive readme
2024-07-02 Forgot to set sockets nonblocking after refactoring
2024-07-09 Increase ODrive timeout and add error checking to ODrive::call functions
    [ODrive.cpp]
2024-07-09 Add BOM and file with linux commands
    [BOM.ods]
2024-07-09 Fix control ui title
    [control_ui.cpp]
2024-07-09 Check ODrive fw is Milana
2024-07-10 Fix ODrive data corruption by setting ack to true
    [ODrive.cpp]
2024-07-10 leg encoder out of position now results in zombie mode, not abrupt stop.
2026-03-17 Include Metal plate to fixate hip servos to gear in BOM
    [BOM.ods]
2026-03-17 Include uart_use_ascii_protocol = False in odrive/readme.md
2026-03-24 Add vaseline to BOM
    [BOM.ods]
